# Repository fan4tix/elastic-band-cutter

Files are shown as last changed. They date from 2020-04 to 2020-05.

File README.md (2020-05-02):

# Automated Elastic Band Cutter

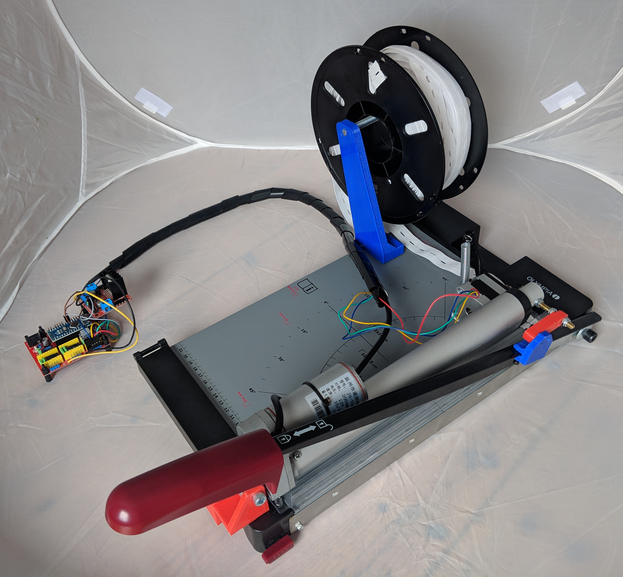
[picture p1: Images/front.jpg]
Elastic Band Cutter


This machine was created during the 2020 Covid-19 pandemic to cut elastic bands for 3D-printed faceshields. I used stuff I had lying around to build the machine as fast as possible so it might not be the fastest, best and prettiest design, but I thought I'd share the design anyways as Inspiration for other people in need of a similar machine.

It is licensed unter CC-BY. Feel fee to use, share and modify the design to your needs.

Watch it working in the following Video:

Automated Elastic Band Cutter Video (http://www.youtube.com/watch?v=ZVcDNM6GSuA "")

## Bill of Materials

### Hardware
* 1 Paper / Photo Cutter (I used an old [Olympia Vario duplex 4600](https://www.amazon.de/Olympia%C2%AE-Papierschneider-Vario-duplex-4600/dp/B078HTYYCR) wich is sadly no longer available)
* 1 [Nema17 2-Phase Stepper](https://www.aliexpress.com/item/4000329570564.html) (I used a cheap 1A version)
* 1 Stepper Driver (e.g. [DRV8825](https://www.aliexpress.com/item/4000857272596.html))
* 1 [Arduino Nano CNC Shield](https://www.aliexpress.com/item/32811233196.html)
* 1 [Arduino Nano](https://www.aliexpress.com/item/32866959979.html)
* 1 [L298D Motor Driver](https://www.aliexpress.com/item/32994608743.html)
* 1 [12V 2A Power Supply](https://www.aliexpress.com/item/33014935336.html)
* 1 [12V Linear Actuator](https://www.aliexpress.com/item/4000655541787.html) (Mine has 200mm stroke length and 750N)
* 1 [3D-Printer Extruder Wheel](https://www.aliexpress.com/item/32903294855.html) (I used the 26
 teeth steel version because of its coarse teeth)
* 2 [623 Roller Bearings](https://www.aliexpress.com/item/32434009843.html)
* 1 [Small Spring](https://www.aliexpress.com/item/4000422954444.html) (approx. 50mm length)
* Some metric nuts and bolts (Sorry America). I used lots of M3 screws for the "extruder", M6 Hardware for clamping the brackets to the picture trimmer and one M8x100 screw for the filament holder)
* Old Filament Spools for winding up the band
* Some wires for hooking it all up

### Printed Parts
Just print all .stl files in the CAD/STL folder. I used PET-G with 4 Perimeters, 0.5mm layer height and 15% infill with a 0.8mm nozzle for all parts. If you are using a 0.4mm nozzle, the layer height should not exceed 0.3mm

## Assembly
The machine consists of three subassemblies. The extruder for advancing the band forward, the cutter for actually cutting the tape and a spool holder for the spools.
Should you need more details on some parts I have missed, try looking at the pictures and renders in `./Images`
### The Extruder
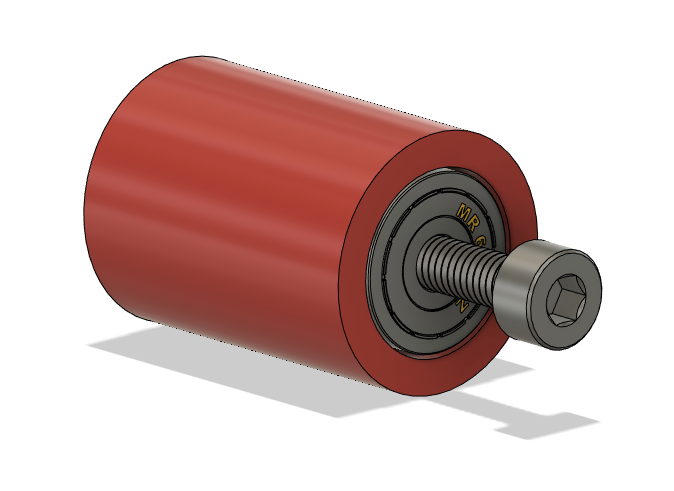
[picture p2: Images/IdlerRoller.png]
Idler Roller


Start by pressing the Bearings into the idler roller (red). After that, install the roller into the idler lever (green) using a M3x30 screw.

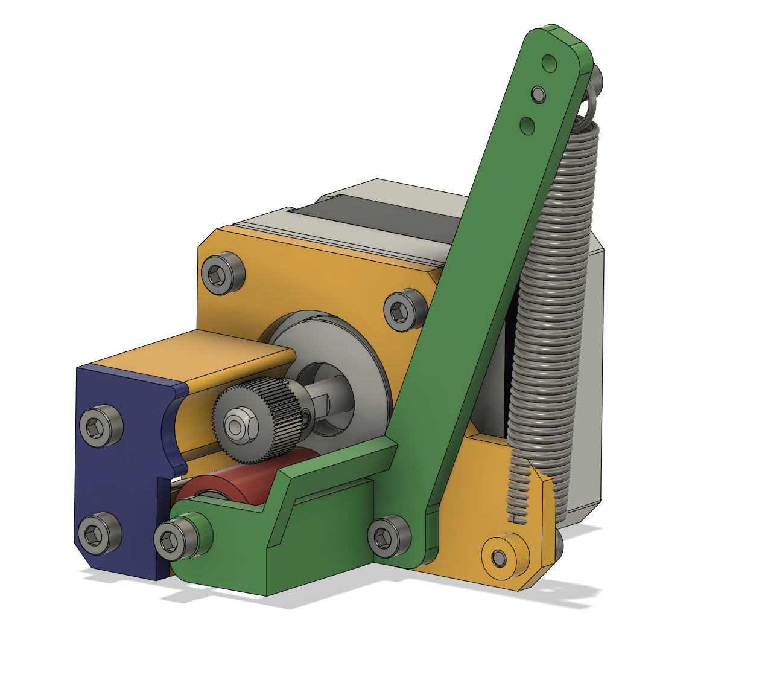
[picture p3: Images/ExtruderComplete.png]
The complete extruder (render)

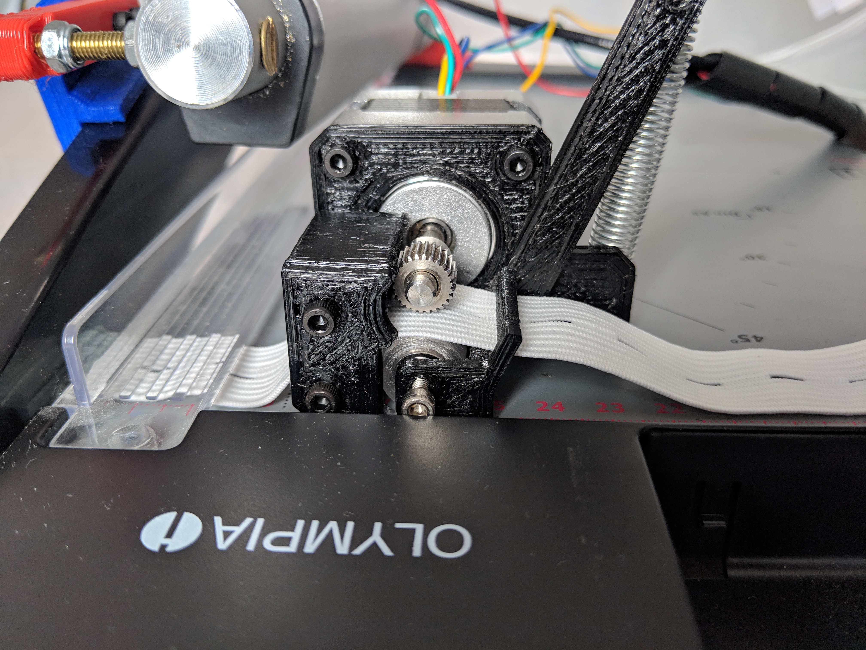
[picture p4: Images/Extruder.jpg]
The complete extruder


Install the NemaPlate (yellow) on the stepper with M3x6 screws. Use one M3x8 Screw to fix the idler lever to the stepper. Don't tighten the screw too much or the lever won't be able to move. Use some Loctite if the screw comes loose after some time.
After that, you can install the cover plate and the spring as shown in the picture.
You can adjust the spring tension by using different holes at the end of the lever.
I just taped the extruder motor to the surface of the paper cutter.
Make sure you place it near the axis of rotation

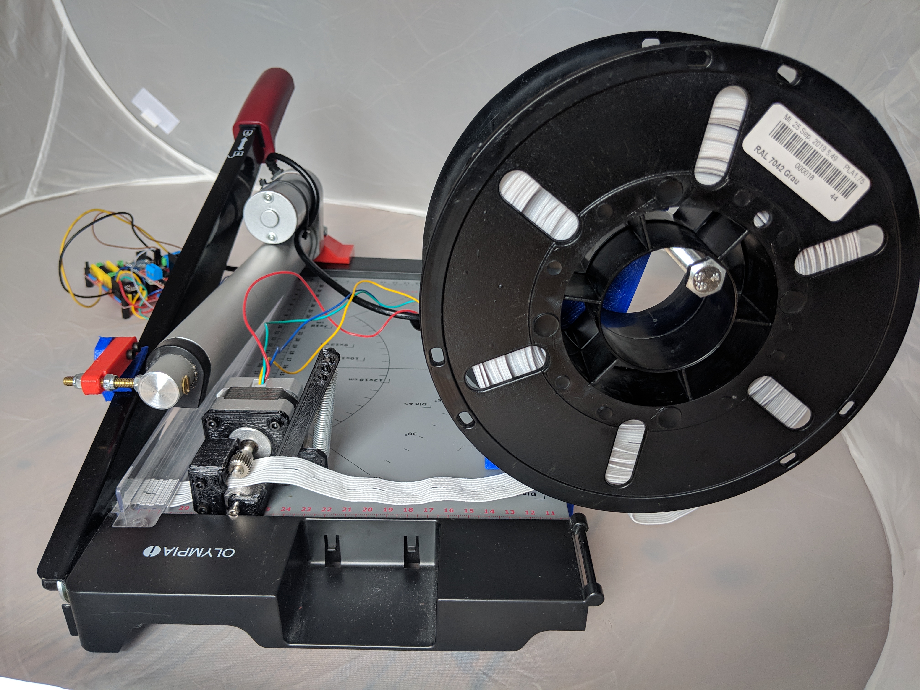
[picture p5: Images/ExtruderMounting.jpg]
Extruder mounting position


### The Cutter

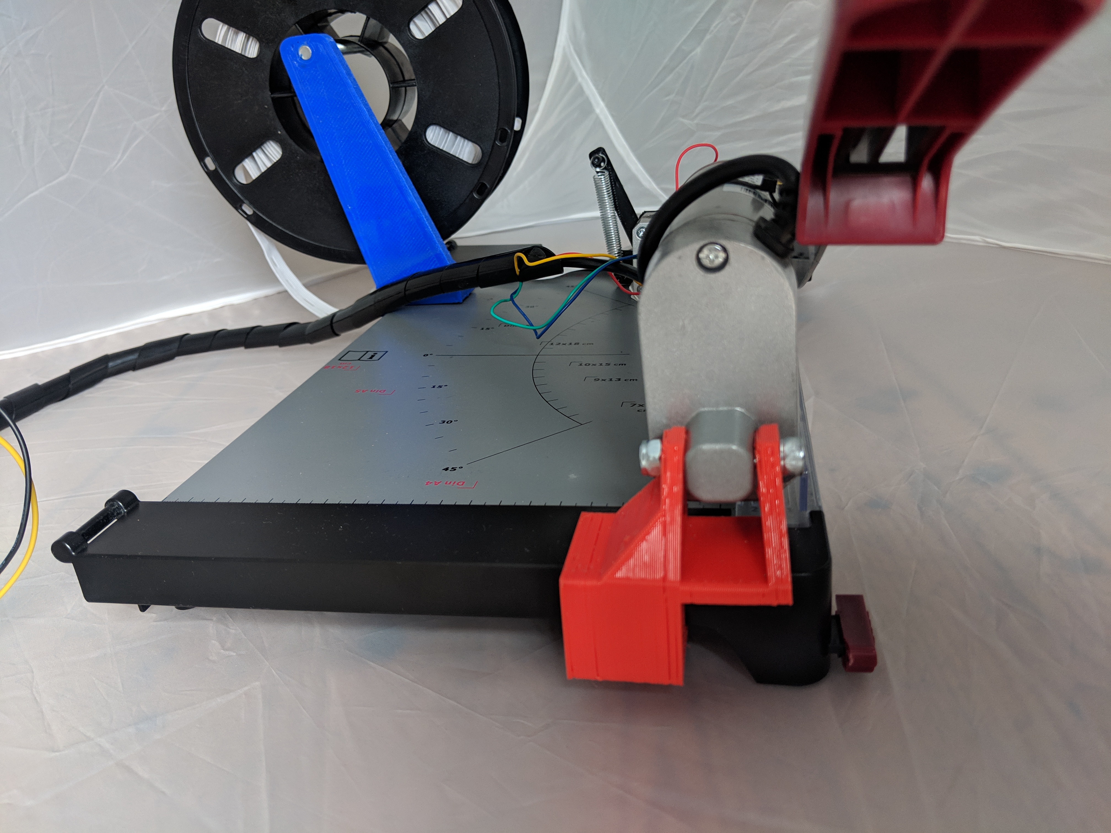
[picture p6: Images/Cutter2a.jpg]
Lower Cutter Bracket


Assemble the lower bracket as shown in the picture. The lower screw is used to fix the bracket to the picture cutter. The upper screw mounts the linear actuator to the bracket.

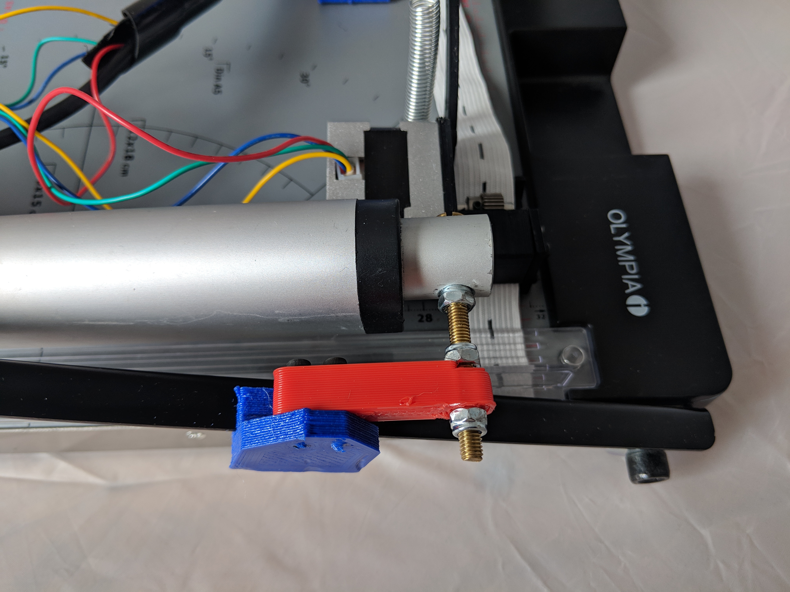
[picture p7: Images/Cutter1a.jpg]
Upper cutter Bracket


The upper bracket consists of two printed parts that need to be joined together using M3x8 screws. Fix to the linear actuator using a M6x60 screw an nylon locknuts.
### The Spool Holder

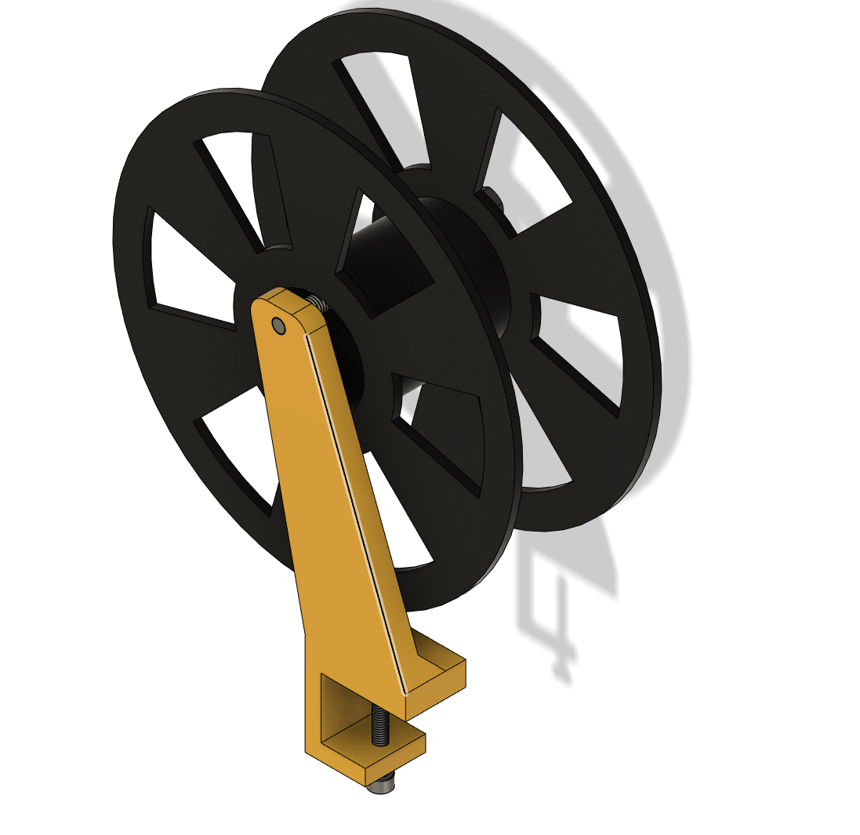
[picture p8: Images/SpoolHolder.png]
Spool Holder


Use a M6x40 Screw to clamp the spool holder to the picture cutter. The spool is hanged from a M8x100 screw that needs to bee installed at the top.

### Electronics

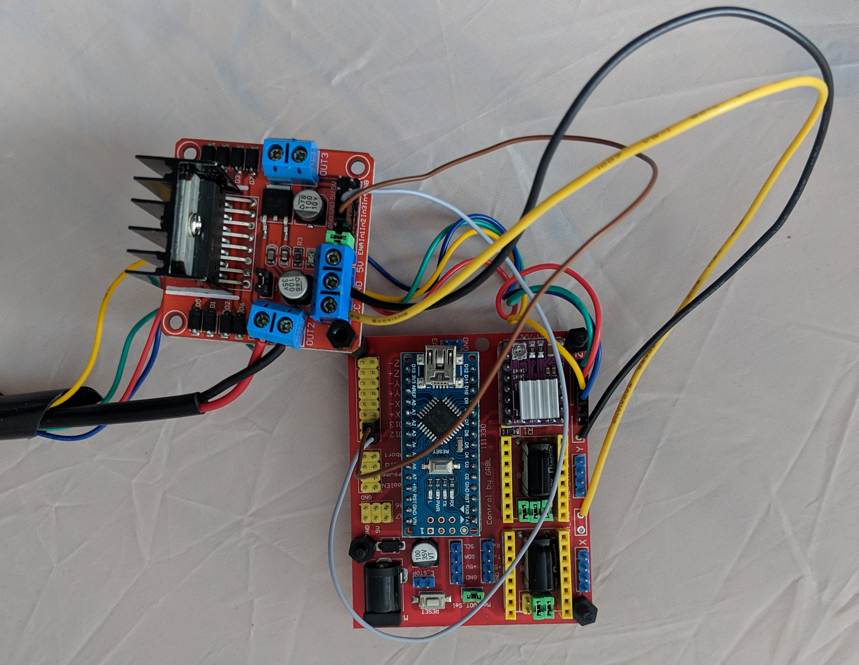
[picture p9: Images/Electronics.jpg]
Electronics assembly


Install the Arduino and the stepper driver on the shield. Use the Z-Axis stepper socket. Connect MOT_GND and MOT_VCC of the shield to the L298's power supply and connect pins 12 and 13 on the shield to the IN1 and IN2 pin of the L298. Afterwards, use the screw terminals on out1 and out2 to connect the linear actuator.

### Code
Just flash the code provided in the "Code" directory to the Arduino. The length of the band is set via the `BAND_LENGTH` define in the Sketch. A means of setting the length via a display and encoder would be great but is not available yet.

If your cuts turn out to be to long or short, try modifying the `stepsPerMM` define to tweak the band length.

## Thanks

Models used in the CAD file
https://grabcad.com/library/623-zz-e3d-titan-idler-bearing-1

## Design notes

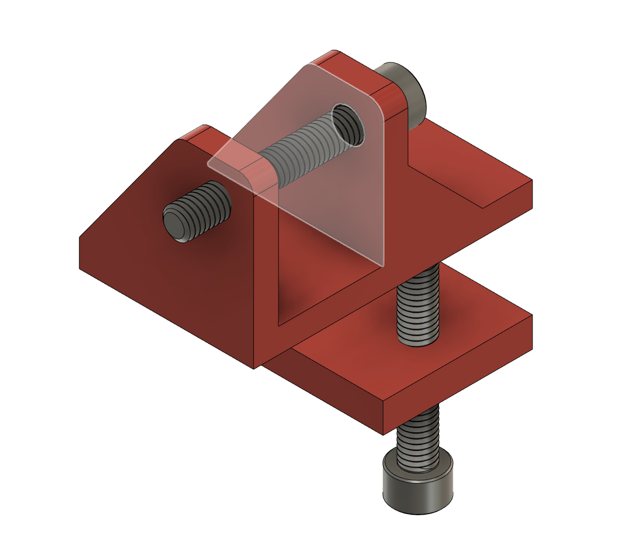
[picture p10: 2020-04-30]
Images/Cutter2.png

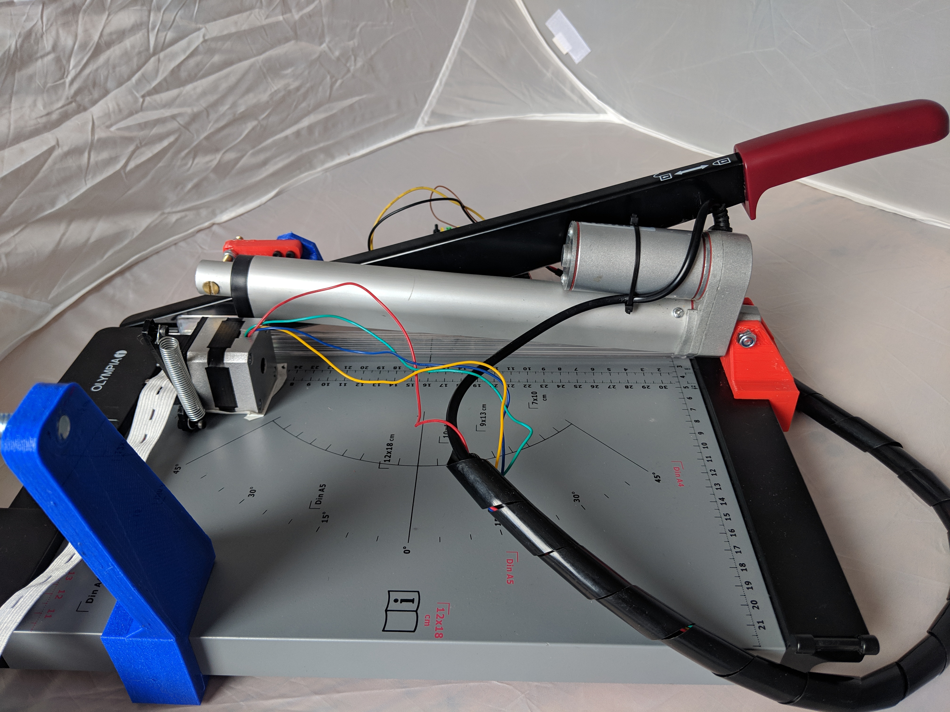
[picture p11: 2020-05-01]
Images/SideView.jpg

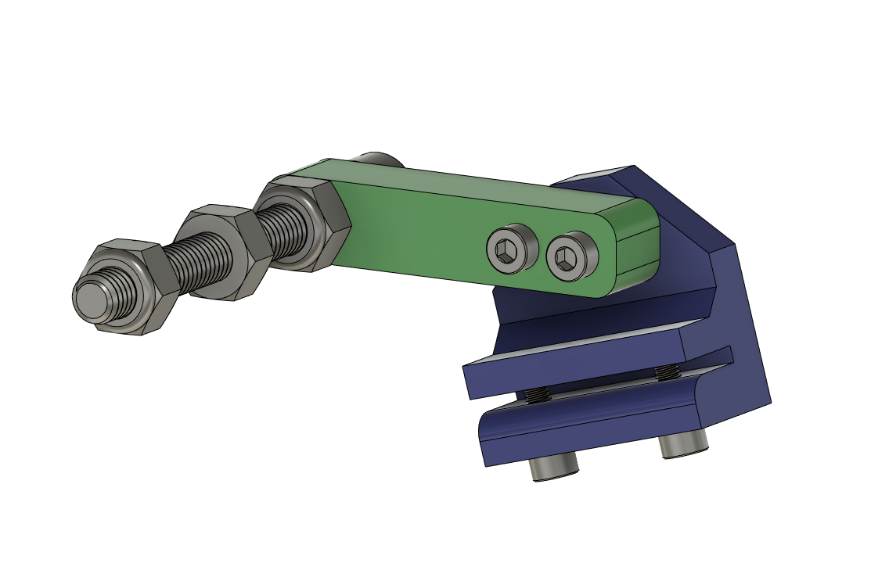
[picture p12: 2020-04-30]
Images/Cutter1.png

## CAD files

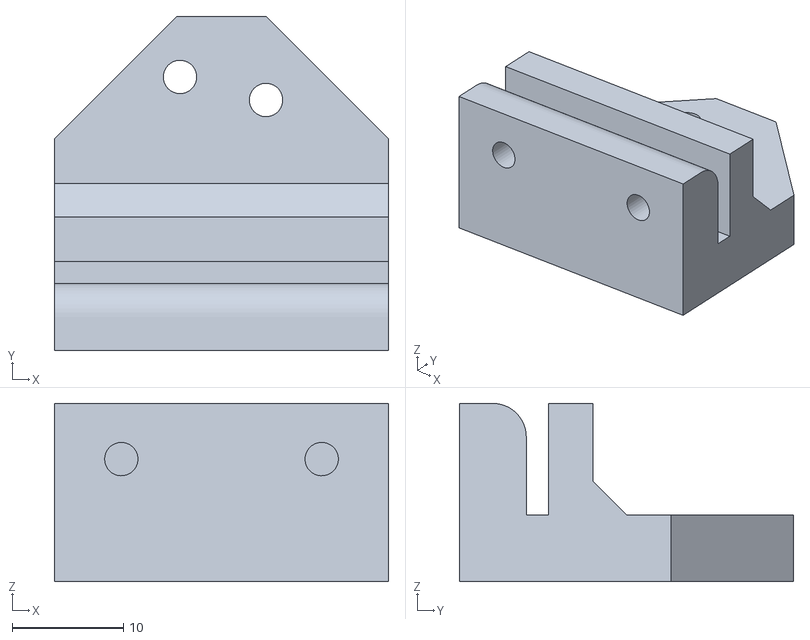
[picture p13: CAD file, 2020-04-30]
CAD/STL/Cutter Bracket.stl
30.0 x 30.0 x 16.0

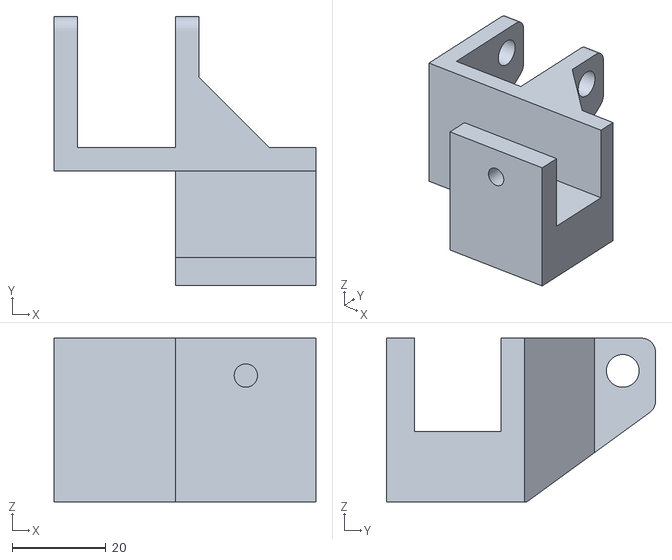
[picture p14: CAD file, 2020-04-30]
CAD/STL/Actuator Bracket Bottom.stl
56.0 x 57.5 x 35.0

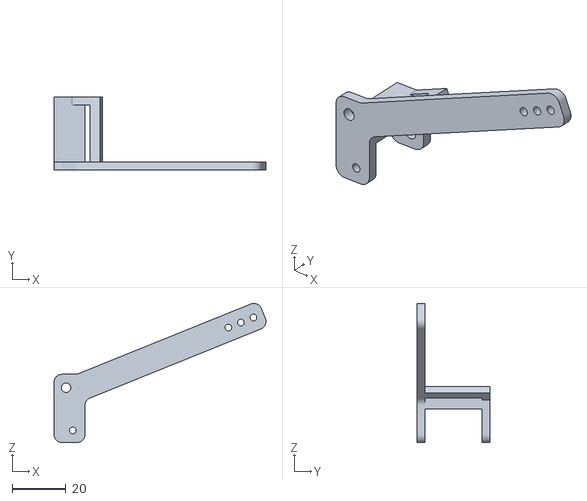
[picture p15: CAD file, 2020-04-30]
CAD/STL/Idler Lever.stl
78.7 x 27.0 x 51.6

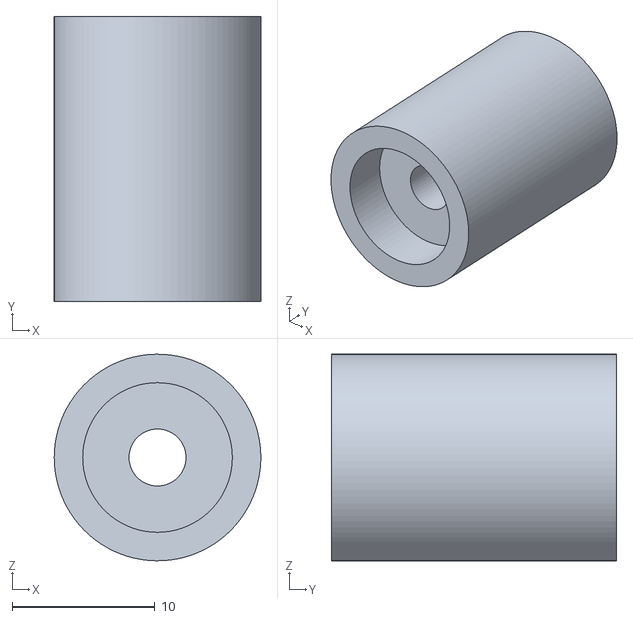
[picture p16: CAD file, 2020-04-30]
CAD/STL/Idler.stl
14.5 x 20.0 x 14.5

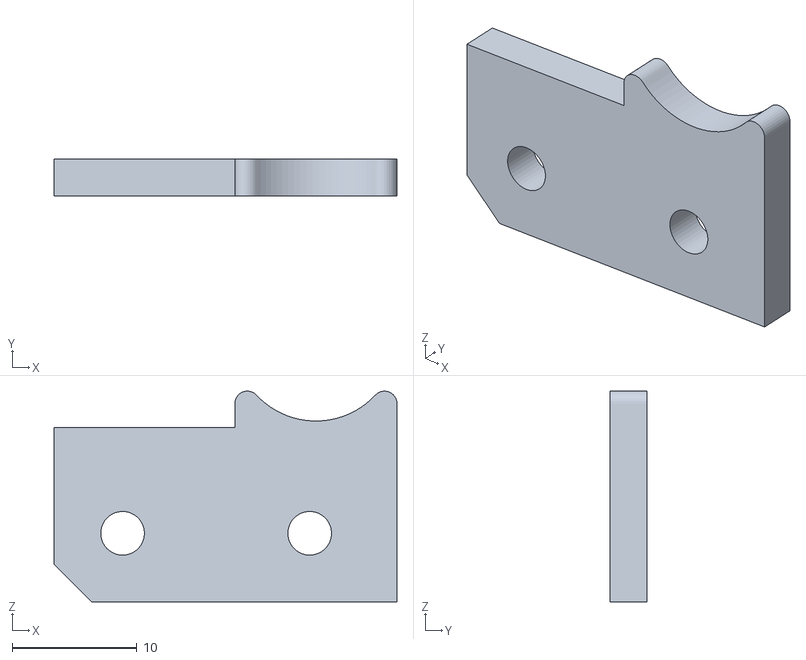
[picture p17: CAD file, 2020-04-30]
CAD/STL/Extruder Cover Plate.stl
27.5 x 3.00 x 16.9

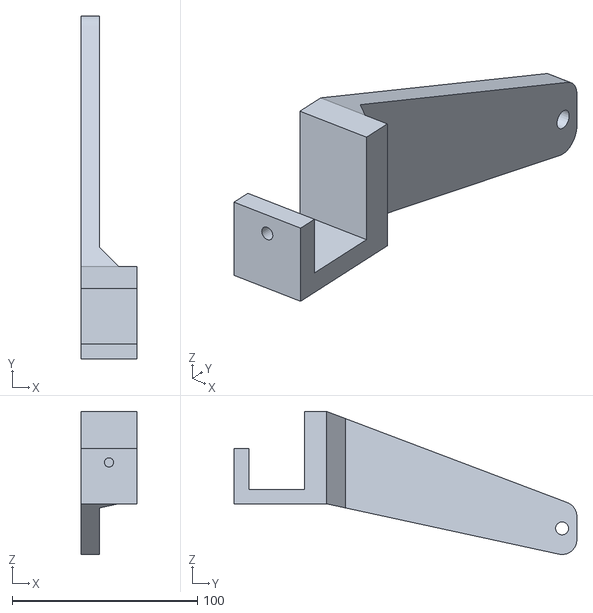
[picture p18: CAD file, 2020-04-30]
CAD/STL/Roll Holder.stl
30.0 x 185.0 x 77.2

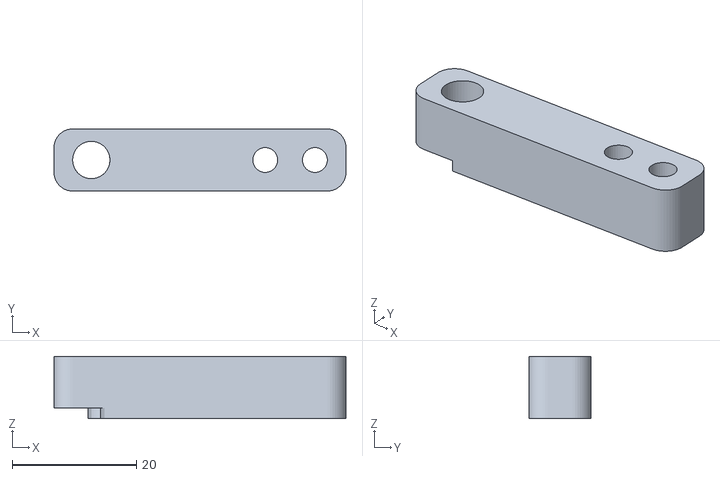
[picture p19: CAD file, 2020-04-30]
CAD/STL/CutterBracketExtension.stl
47.0 x 10.0 x 10.0

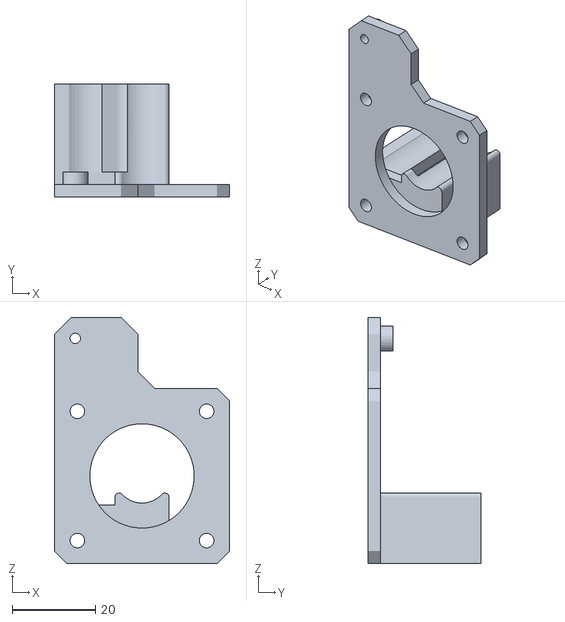
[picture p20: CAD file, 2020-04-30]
CAD/STL/Nema Plate.stl
42.0 x 27.0 x 59.0

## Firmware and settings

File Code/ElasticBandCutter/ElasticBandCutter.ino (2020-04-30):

/*
Elastic Band Cutter
Copyright Martin Schörner

Last Change: 2020-04-30
License: CC BY
*/

// Length of each band. Customize to fit your needs
#define BAND_LENGTH 250

// Steps per mm of extruded band.
// Tweak this value to fit your extruder gear
#define stepsPerMM 6.4

#define stepsPerRevolution 200


// Pin defines for the linear actuator
#define cutterOutPin 12
#define cutterInPin 13

// Pin defines for the steppers
#define dirPin 4
#define stepPin 7
#define enablePin 8


void setup() {
  // Declare pins as output:
  pinMode(stepPin, OUTPUT);
  pinMode(dirPin, OUTPUT);
  pinMode(enablePin, OUTPUT);

  pinMode(cutterOutPin, OUTPUT);
  pinMode(cutterInPin, OUTPUT);

  digitalWrite(cutterOutPin, LOW);
  digitalWrite(cutterInPin, LOW);

  digitalWrite(enablePin, LOW);
}
void loop() {

  digitalWrite(cutterOutPin, HIGH);
  digitalWrite(cutterInPin, LOW);

  delay(6000);
    digitalWrite(cutterOutPin, LOW);
  digitalWrite(cutterInPin, LOW);

  // Set the spinning direction clockwise:
  digitalWrite(dirPin, LOW);
  // Spin the stepper motor 1 revolution slowly:
  for (int i = 0; i < stepsPerMM *  BAND_LENGTH; i++) {
    // These four lines result in 1 step:
    digitalWrite(stepPin, HIGH);
    delayMicroseconds(2000);
    digitalWrite(stepPin, LOW);
    delayMicroseconds(2000);

  }

  digitalWrite(cutterOutPin, LOW);
  digitalWrite(cutterInPin, HIGH);
  delay(6500);


  digitalWrite(cutterOutPin, LOW);
  digitalWrite(cutterInPin, LOW);

  delay(1000);

}

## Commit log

2020-05-01 Updated printing instructions
2020-05-01 Updated assembly instructions, added more images
